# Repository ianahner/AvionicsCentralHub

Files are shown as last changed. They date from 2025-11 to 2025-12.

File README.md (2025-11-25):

# Avionics Central Hub

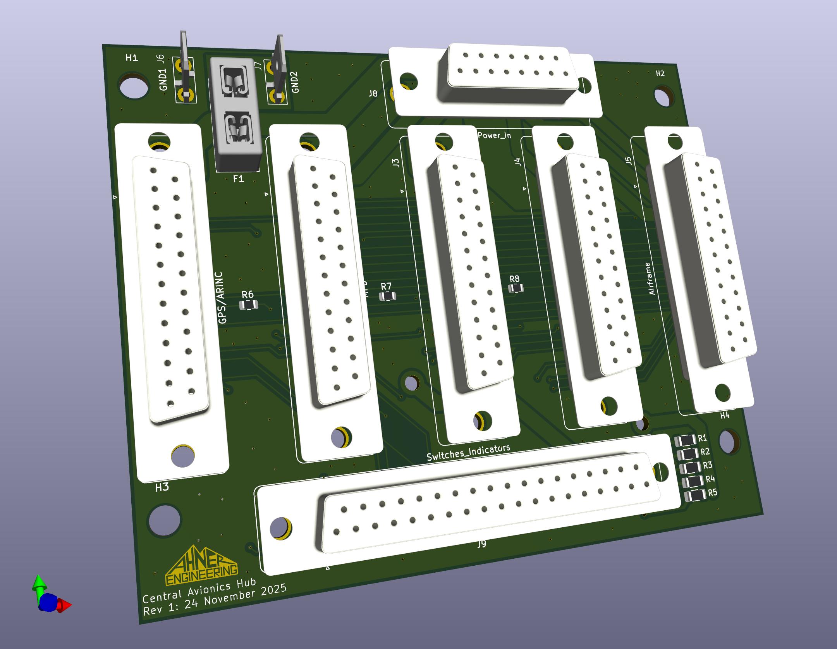
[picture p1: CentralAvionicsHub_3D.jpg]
3D Render


## Design Goals
This project was designed to solve a number of problems encountered while laying out the electrical wiring for an experimental aircraft. I wanted to accomplish the following:
- Single Point Ground for all panel avionics
- Eliminate as many splices as possible from wiring harness
- Simplify harness design, ideally having only a single harness branch to each device
- Allow for easy future expansion or modification if an individual instrument is changed without having to rework significant portions of the harness

## Component Considerations
My panel consists of the following:
- GRT Horizon 10.1 PFD
- GRT Mini G2 MFD
- Garmin GNX375 GPS/XPDR
- Trig TX56A NavCom
- Small Switch and annunciator panel
- GRT Autopilot

## Physical Footprint
The GRT Horizon 10.1 EFIS includes mounting holes on the rear of the display unit for the GRT SafeFly GPS. As I am not using the SafeFly GPS in my build due to having the Garmin, I have made this board fit the mounting hole pattern of that device. This will allow the board to mount directly to the rear of the PFD. 

The board is slightly larger in outside dimensions than the SafeFly, but the mounting holes are the same. When mounting to the rear of the PFD this is no big deal, but if you are mounting in some other tucked away spot be aware of the outside dimensions. 

In the future I plan to design a simple 3D printed cover for this board. I'll add it to this repo if/when that ever happens.

## Audio Mixing Resistors
This audio mixing solution is of course not intended to be a high fidelity audio solution. The intention here is to mix the mono "annunciator" signals from instruments for messages like "AP Disconnect" or "Minimums." I highly discourage anyone from using this solution for something like radio audio or even non-essential music audio as the results are likely to be less than desirable. For the purposes of mixing alert tones, it should be perfectly acceptable.

The resistors exist simply to prevent one audio device from backfeeding the driver of another device. The value was chosen based on the output impedance of the devices I have, but should be reasonable for the vast majority of situations you're likely to encounter. 

As an aside, though this LOOKS extremely hacky (and it sort of is) it comes straight out of the manual for the PSE certified intercom and others, and is a rather common old-school approach to audio mixing, back before engineering was invented. 

## LED Series Resistor values assumptions
The LED series resistors R1-R5 are optional for use with panel mount LEDs that either don't have a series resistor, or have a voltage range that isn't high enough for the 14.5V our alternators tend to run. 

The resistor specified in the BOM below is a 620Ω which was calculated to provide 20mA to a 2V LED assuming a bus voltage of 14.5V. Adjust this to your needs, or simply install a 0Ω jumper. 

## Why does Fuse F1 exist? 
This fuse does not need to exist at all, and you can jumper it in many cases if you do not like the idea of a fuse in your ground. The purpose of that fuse is rather specific to my application. I intend to ground GND1 (J6) directly to battery negative in my aircraft. My aircraft is a composite pusher configuration with the battery in the nose and the engine on the rear. There is a single very large negative battery lead running the length of the fuselage, and the fuselage being composite is of no use for grounding. 

The intention in this application is to run the secondary fused ground all the way back to the grounding stud where the primary alternator is grounded. This protects against any failure of the main battery negative or of the GND1 connection to the battery. 

I have included the fuse to protect against a very unlikely fault condition where that main ground lead to the rear of the airplane is damaged, or the engine to firewall bonding strap is broken. In that case if a pilot were to attempt to start the aircraft, the starter current could try to go through this board. That would not only blow the traces off the board, but also potentially damage the relatively small #12 or #10 wire used for this redundant ground. 

The fuse should be sized to protect the wire, assumed to be 20-30A. If a ground strap is broken and a pilot tries to start the plane, the fuse will blow. The pilot will also be unable to start the plane, so this should be sign enough to troubleshoot the problem, and then replace the fuse. A fuse is fine here instead of a CB because there is no reasonable situation where this would blow in flight that could be fixed by resetting a CB. 

## BOM for Population
QTY | DK PN | REFs
--- | --- | ---
1 | 36-3568-ND | F1
1 | A35173-ND | J8
5 | A35183-ND | J1, J2, J3, J4, J5
1 | A35186-ND | J9
2 | 63824 | J6, J7
5 | 541-RCP1206W620RFEACT-ND | R1, R2, R3, R4, R5
3 | RMCF0805JT470RCT-ND | R6, R7, R8

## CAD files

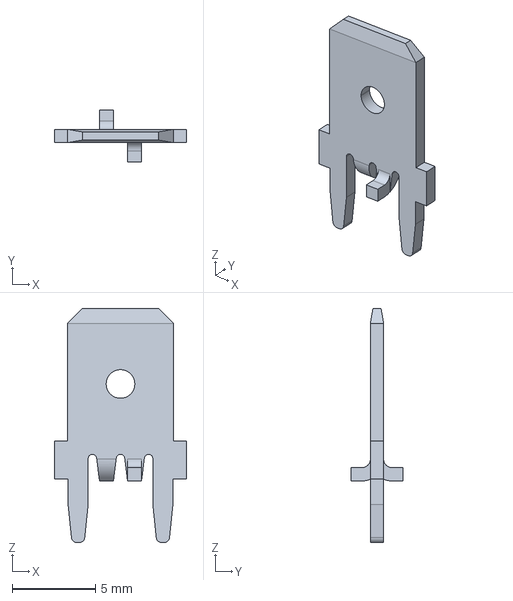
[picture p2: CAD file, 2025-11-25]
3D Models/c-63824-5-ad-3d.stp
7.92 x 3.09 x 14.0 mm

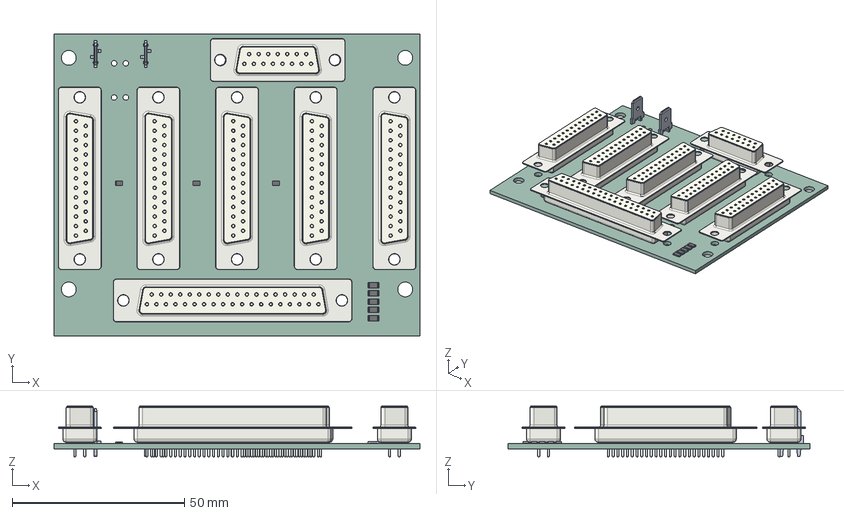
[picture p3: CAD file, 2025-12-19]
CentralAvionicsHub.step
106.4 x 87.9 x 14.7 mm
R_0805_2012Metric x 3
DSUB-37_Socket_Vertical_P2.77x2.84mm_MountingHoles
c-63824-5-ad-3d x 2
R_1206_3216Metric x 5
DSUB-25_Socket_Vertical_P2.77x2.84mm_MountingHoles x 5
DSUB-15_Socket_Vertical_P2.77x2.84mm_MountingHoles
CentralAvionicsHub_PCB

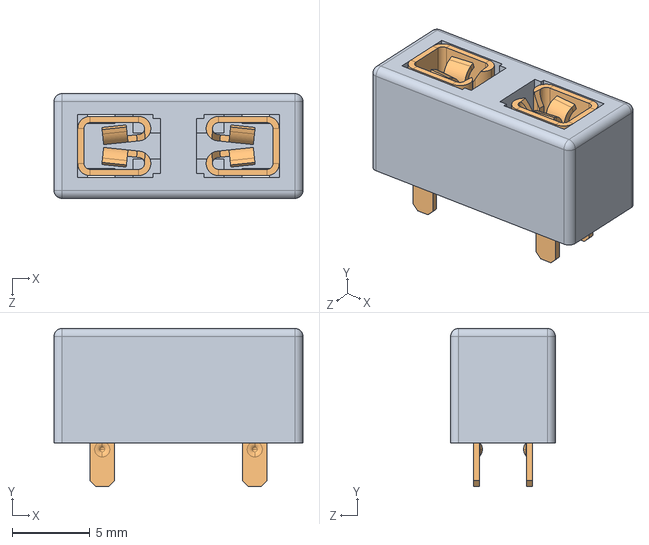
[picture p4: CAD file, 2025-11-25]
3D Models/3568.step
16.0 x 10.2 x 6.73 mm
F3568-1
3557_rev.C x 2

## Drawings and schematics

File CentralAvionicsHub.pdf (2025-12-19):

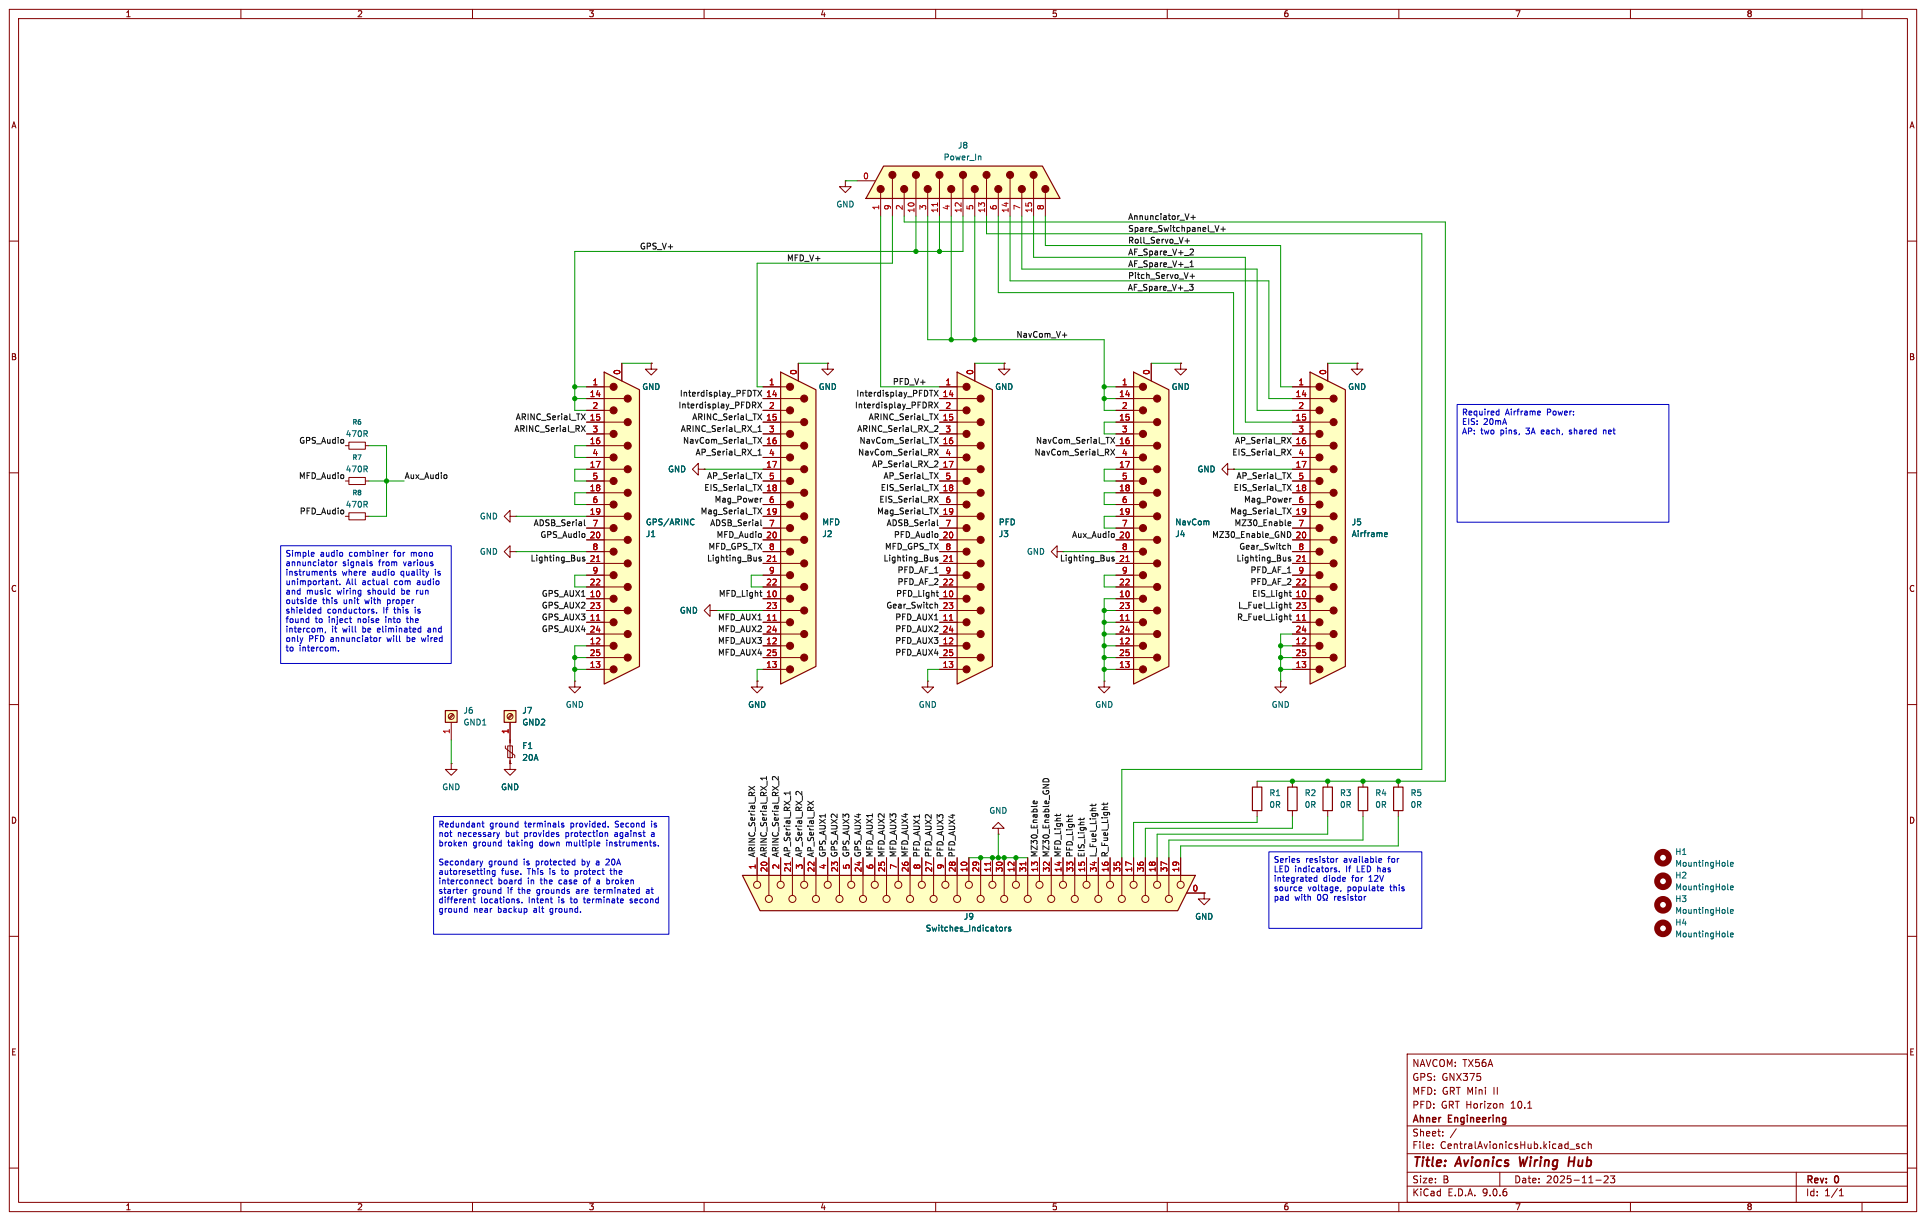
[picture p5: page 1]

and music wiring should be run

found to inject noise into the

H1 MountingHole H4 MountingHole GND GND

ground near backup alt ground.

Id: 1/1 Title: Avionics Wiring Hub

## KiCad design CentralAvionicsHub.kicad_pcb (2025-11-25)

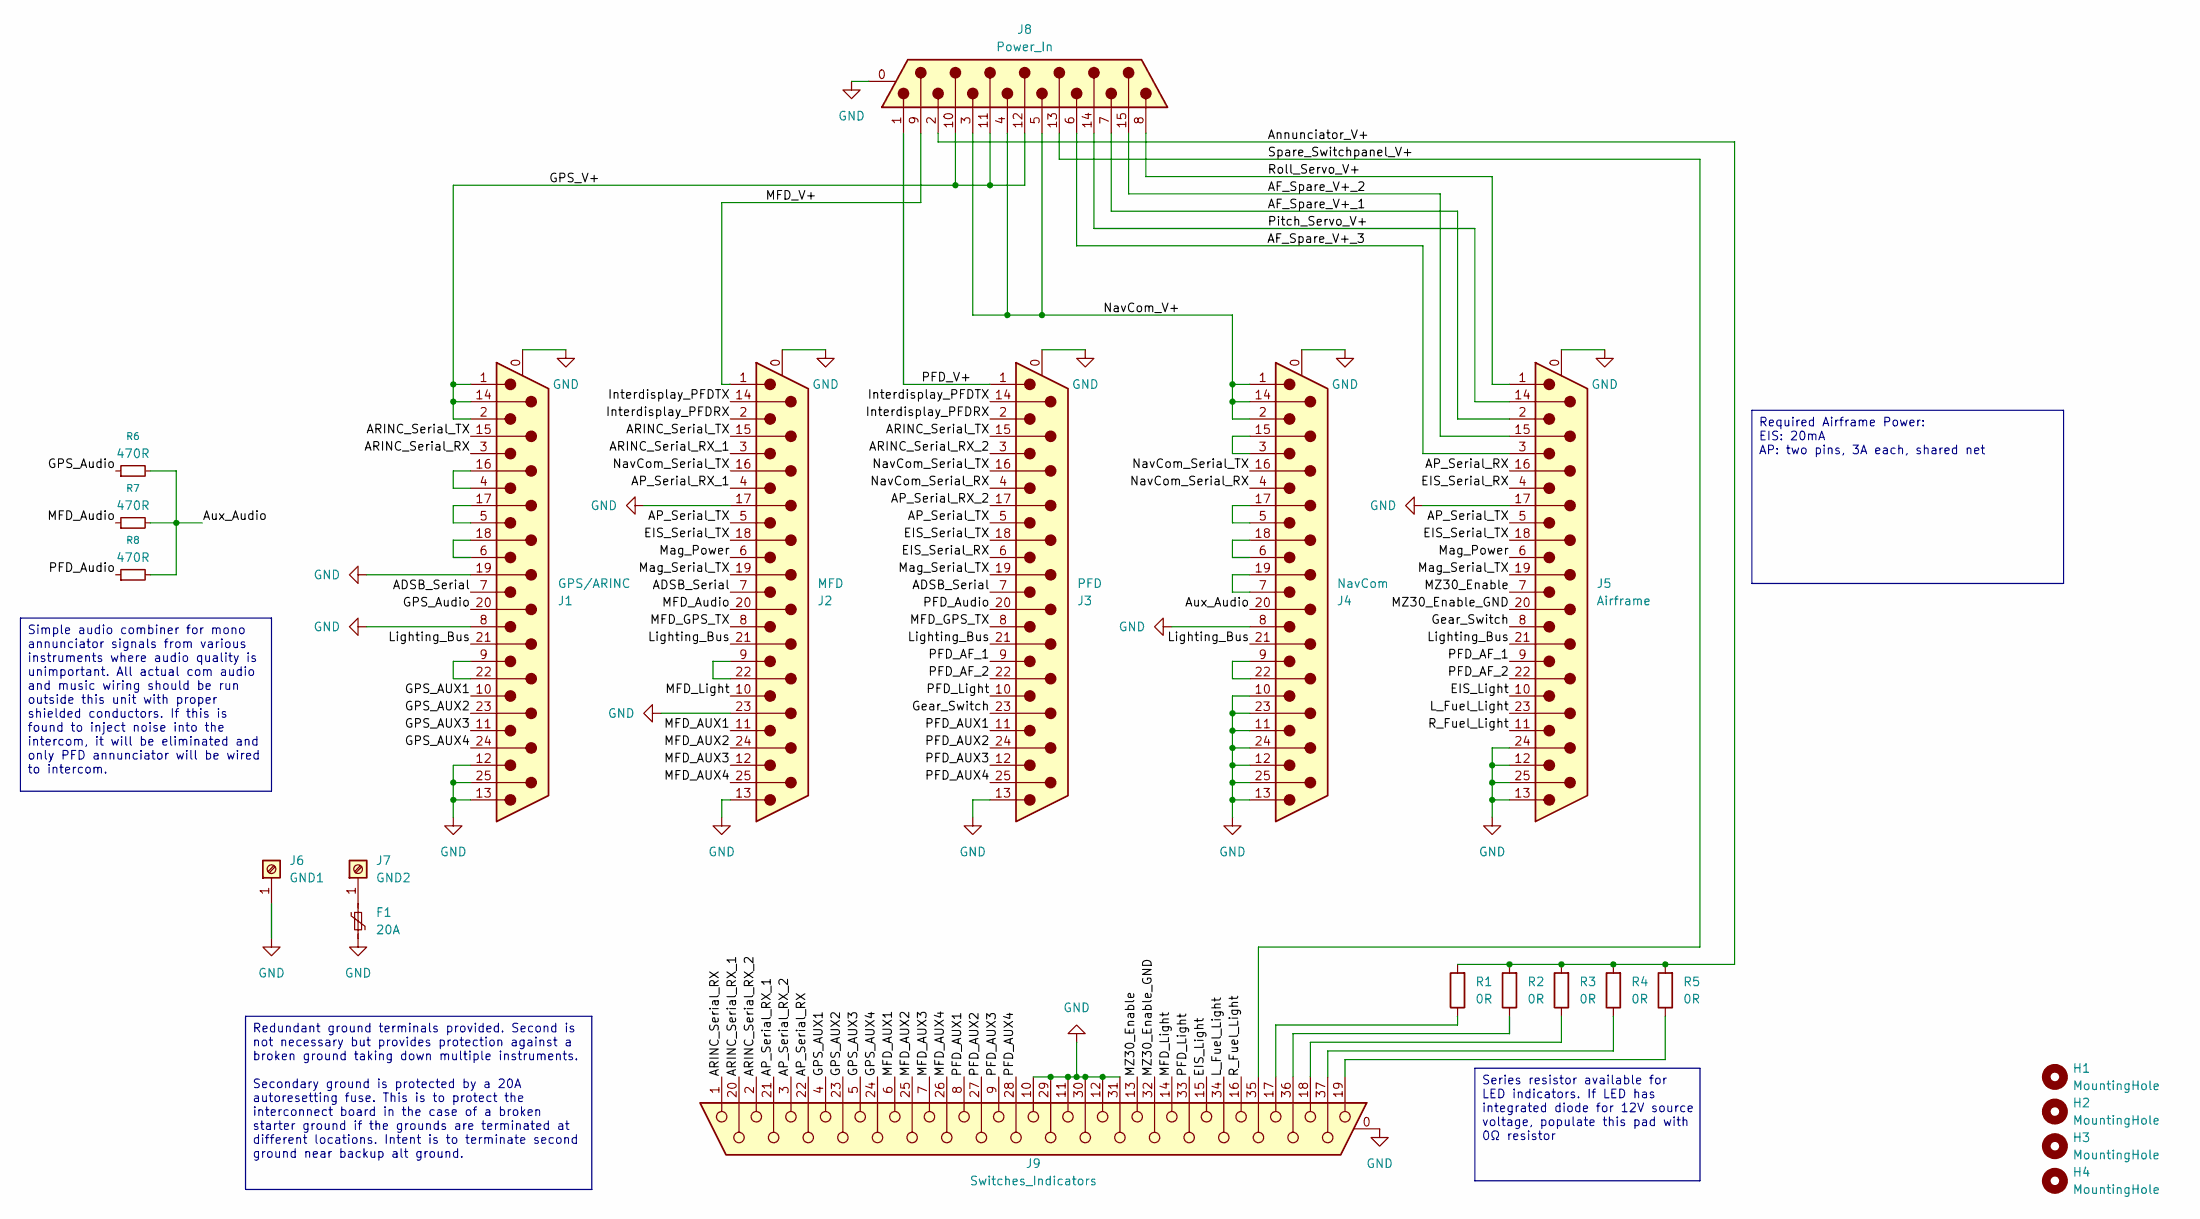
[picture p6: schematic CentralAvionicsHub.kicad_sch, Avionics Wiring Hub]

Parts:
F1: 20A; FUSE_3568
H1, H2, H3, H4: MountingHole; MountingHole_4.3mm_M4_ISO7380
J1: GPS/ARINC; DSUB-25_Socket_Vertical_P2.77x2.84mm_MountingHoles
J2: MFD; DSUB-25_Socket_Vertical_P2.77x2.84mm_MountingHoles
J3: PFD; DSUB-25_Socket_Vertical_P2.77x2.84mm_MountingHoles
J4: NavCom; DSUB-25_Socket_Vertical_P2.77x2.84mm_MountingHoles
J5: Airframe; DSUB-25_Socket_Vertical_P2.77x2.84mm_MountingHoles
J6: GND1; 63824
J7: GND2; 63824
J8: Power_In; 5787683 15 Pin Female Vertical
J9: Switches_Indicators; DSUB-37_Socket_Vertical_P2.77x2.84mm_MountingHoles
R1, R2, R3, R4, R5: 0R; R_1206_3216Metric_Pad1.30x1.75mm_HandSolder
R6, R7, R8: 470R; R_0805_2012Metric

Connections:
/ADSB_Serial: J1.7, J2.7, J3.7
/AF_Spare_V+_1: J5.2, J8.7
/AF_Spare_V+_2: J5.15, J8.15
/AF_Spare_V+_3: J5.3, J8.6
/AP_Serial_RX: J5.16, J9.22
/AP_Serial_RX_1: J2.4, J9.21
/AP_Serial_RX_2: J3.17, J9.3
/AP_Serial_TX: J2.5, J3.5, J5.5
/ARINC_Serial_RX: J1.3, J9.1
/ARINC_Serial_RX_1: J2.3, J9.20
/ARINC_Serial_RX_2: J3.3, J9.2
/ARINC_Serial_TX: J1.15, J2.15, J3.15
/Annunciator_V+: J8.2, R1.2, R2.2, R3.2, R4.2, R5.2
/Aux_Audio: J4.20, R6.2, R7.2, R8.2
/EIS_Light: J5.10, J9.15
/EIS_Serial_RX: J3.6, J5.4
/EIS_Serial_TX: J2.18, J3.18, J5.18
/GPS_AUX1: J1.10, J9.4
/GPS_AUX2: J1.23, J9.23
/GPS_AUX3: J1.11, J9.5
/GPS_AUX4: J1.24, J9.24
/GPS_Audio: J1.20, R6.1
/GPS_V+: J1.1, J1.2, J1.14, J8.10, J8.11 (P111), J8.12
/Gear_Switch: J3.23, J5.8
/Interdisplay_PFDRX: J2.2, J3.2
/Interdisplay_PFDTX: J2.14, J3.14
/L_Fuel_Light: J5.23, J9.34
/Lighting_Bus: J1.21, J2.21, J3.21, J4.21, J5.21
/MFD_AUX1: J2.11, J9.6
/MFD_AUX2: J2.24, J9.25
/MFD_AUX3: J2.12, J9.7
/MFD_AUX4: J2.25, J9.26
/MFD_Audio: J2.20, R7.1
/MFD_GPS_TX: J2.8, J3.8
/MFD_Light: J2.10, J9.14
/MFD_V+: J2.1, J8.9
/MZ30_Enable: J5.7, J9.13
/MZ30_Enable_GND: J5.20, J9.32
/Mag_Power: J2.6, J5.6
/Mag_Serial_TX: J2.19, J3.19, J5.19
/NavCom_Serial_RX: J3.4, J4.4
/NavCom_Serial_TX: J2.16, J3.16, J4.16
/NavCom_V+: J4.1, J4.2, J4.14, J8.3, J8.4, J8.5
/PFD_AF_1: J3.9, J5.9
/PFD_AF_2: J3.22, J5.22
/PFD_AUX1: J3.11, J9.8
/PFD_AUX2: J3.24, J9.27
/PFD_AUX3: J3.12, J9.9
/PFD_AUX4: J3.25, J9.28
/PFD_Audio: J3.20, R8.1
/PFD_Light: J3.10, J9.33
/PFD_V+: J3.1, J8.1
/Pitch_Servo_V+: J5.14, J8.14
/R_Fuel_Light: J5.11, J9.16
/Roll_Servo_V+: J5.1, J8.8
/Spare_Switchpanel_V+: J8.13, J9.35
GND: F1.2, J1.0 (PAD), J1.8, J1.12, J1.13, J1.19, J1.25, J2.0 (PAD), J2.13, J2.17, J2.23, J3.0 (PAD), J3.13, J4.0 (PAD), J4.8, J4.10, J4.11, J4.12, J4.13, J4.23, J4.24, J4.25, J5.0 (PAD), J5.12, J5.13, J5.17, J5.24, J5.25, J6.1, J8.0 (PAD), J9.0 (PAD), J9.10, J9.11, J9.12, J9.29, J9.30, J9.31
unnamed: J1.4, J1.16
unnamed: J1.5, J1.17
unnamed: J1.6, J1.18
unnamed: J1.9, J1.22
unnamed: J2.9, J2.22
unnamed: J4.3, J4.15
unnamed: J4.5, J4.17
unnamed: J4.6, J4.18
unnamed: J4.7, J4.19
unnamed: J4.9, J4.22
unnamed: F1.1, J7.1
unnamed: J9.17, R1.1
unnamed: J9.18, R3.1
unnamed: J9.19, R5.1
unnamed: J9.36, R2.1
unnamed: J9.37, R4.1

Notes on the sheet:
Simple audio combiner for mono annunciator signals from various instruments where audio quality is unimportant. All actual com audio and music wiring should be run outside this unit with proper shielded conductors. If this is found to inject noise into the intercom, it will be eliminated and only P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
Required Airframe Power: EIS: 20mA AP: two pins, 3A each, shared net
Redundant ground terminals provided. Second is not necessary but provides protection against a broken ground taking down multiple instruments. Secondary ground is protected by a 20A autoresetting fuse. This is to protect the interconnect board in the case of a broken starter ground if the grounds a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
Series resistor available for LED indicators. If LED has integrated diode for 12V source voltage, populate this pad with 0Ω resistor

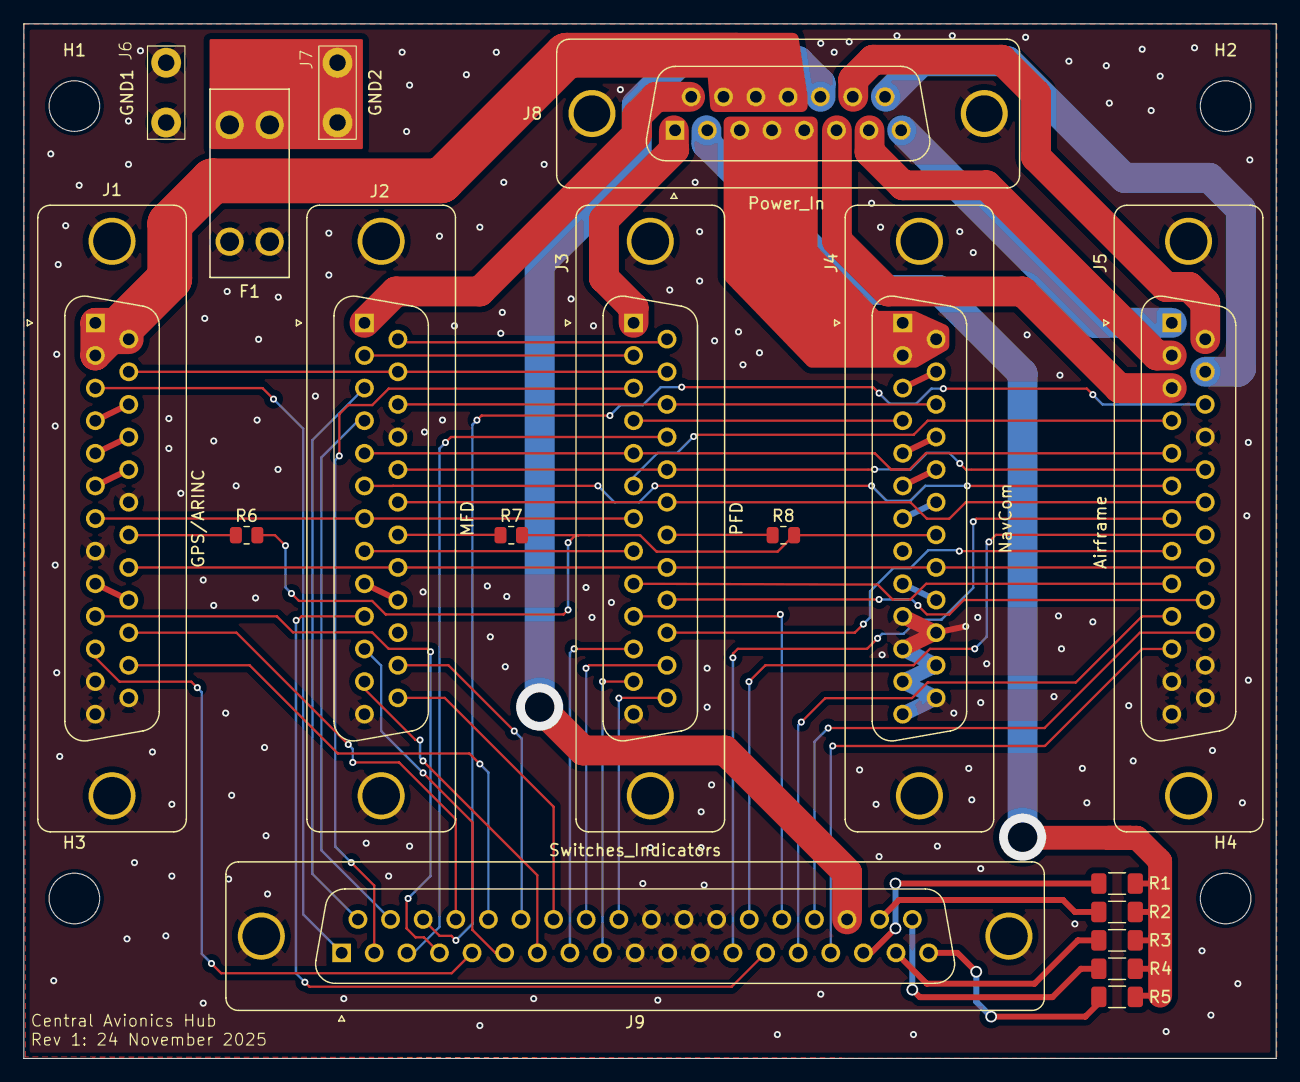
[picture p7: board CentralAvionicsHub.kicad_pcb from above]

Board: 2 copper layers, 106.4 x 87.9 mm, 22 parts (0 on the bottom side), 73 nets.

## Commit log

2025-11-14 Schematic mostly finalized, preliminary board layout for basic space testing and sanity checking
    [CentralAvionicsHub.kicad_sch]
2025-11-14 Basic layout commit
    [CentralAvionicsHub.kicad_pcb]
2025-11-17 Added mounting holes, aligned components, began power layout with properly sized traces.
    [CentralAvionicsHub.kicad_pcb, CentralAvionicsHub.kicad_sch]
2025-11-18 Power routing mostly complete. Rearranged pinout on power_in connector to support better routing. Broke a number of other traces in the process, will correct later.
    [CentralAvionicsHub.kicad_pcb, CentralAvionicsHub.kicad_sch]
2025-11-18 Removed Curved Traces
    [CentralAvionicsHub.kicad_pcb]
2025-11-18 Trace cleanup
    [CentralAvionicsHub.kicad_pcb]
2025-11-19 Refined layout. Still need to address gnd connector
    [CentralAvionicsHub.kicad_pcb]
2025-11-24 Minor Fixes, silkscreen updates.
    [CentralAvionicsHub.kicad_pcb, CentralAvionicsHub.kicad_sch]
2025-11-24 Changed Ground connections to 250 FASTON tabs. Updated silkscreen. Corrected minor DRC errors.
    [CentralAvionicsHub.kicad_pcb, CentralAvionicsHub.kicad_sch]
2025-11-24 Generated Gerbers
    [CentralAvionicsHub-B_Cu.gbl, CentralAvionicsHub-B_Mask.gbs, CentralAvionicsHub-B_Paste.gbp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]
2025-11-24 Zipped Gerbers, Added 3D render
2025-11-25 Replaced F1 footprint with traditional fuseholder for Mini Blade Fuse.
    Changed R1-R5 to 1206
    Modified footprint of DA15 to match TE part
    Managed Libraries, regenerated gerbers at V1.
    [3568.step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]
2025-12-19 Replot PDFs and 3d model
    [CentralAvionicsHub.step]
